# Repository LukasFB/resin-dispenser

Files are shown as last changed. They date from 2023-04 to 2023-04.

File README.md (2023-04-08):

# electronic parts

Arduino Uno (or any other 5V model with I2C and at least 12 free pins)

100g load cell:
https://www.amazon.com/a11112800ux0213-Electronic-Four-wire-Connecting-Weighing/dp/B00880RSTK

HX711 amplifier:
https://www.amazon.com/Comimark-Weighing-Dual-Channel-Precision-Pressure/dp/B07X2JZRKB

2x stepper motor drivers (A4988 is fine, TMC2209 if you're feeling fancy):
https://www.amazon.com/Stepstick-Stepper-Compatible-Printer-Robotics/dp/B09PHD1TR9

2x Nema 17 stepper motors:
https://www.amazon.com/Usongshine-Nema17-Stepper-17HS4401S-Printer/dp/B07KW7F3P9?th=1

2x 100uF capacitors

16x2 LCD with I2C backpack:
https://www.amazon.com/Weewooday-Interface-Backlight-Compatible-MEGA2560/dp/B08MPTND1V?th=1

Toggle switch:
https://www.amazon.com/Nilight-Rocker-Toggle-Switch-Waterproof/dp/B078KBC5VH

4x MX switches

12V, 2A power supply

# mechanical parts
silicone tubing 5mm OD 3mm ID:
https://www.amazon.com/ANPTGHT-Silicone-High-temperature-Brewing-Transfer/dp/B08SQQDZMK?th=1

6x 608 bearings:
https://www.amazon.com/608-2RS-Skateboard-Bearing-Rolling-bearings/dp/B073ST742Z

2x 20 tooth GT2 pulley, 5mm bore:
https://www.amazon.com/3Dman-Pulley-Timing-Aluminum-Printer/dp/B085XLRXS1

2x resin bottles, no bigger than 90x90mm and 220mm tall, about 1 liter:
https://www.amazon.com/Othmro-Plastic-Storage-Container-Translucent/dp/B0828G27TH?th=1

M3 hardware

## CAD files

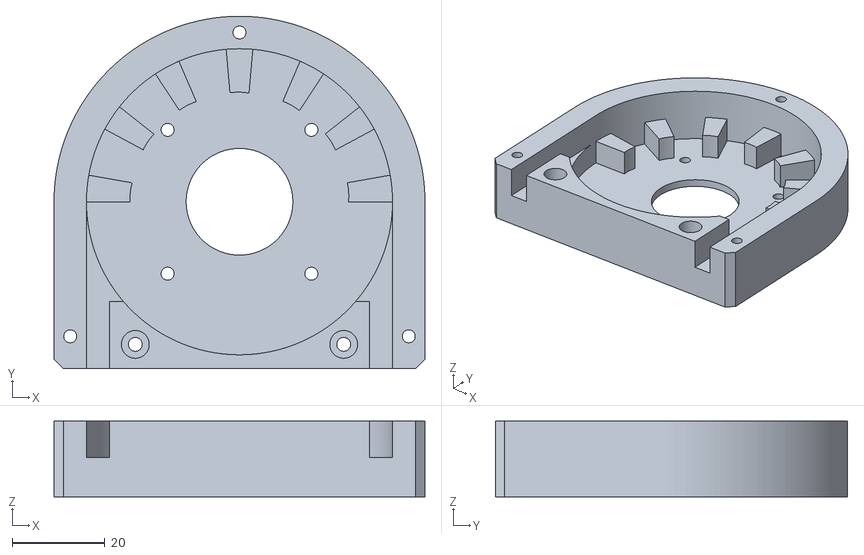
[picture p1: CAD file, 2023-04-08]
printed parts/p_resin dispenser 2 v10_pump_1_housing.stl
80.0 x 76.0 x 16.4

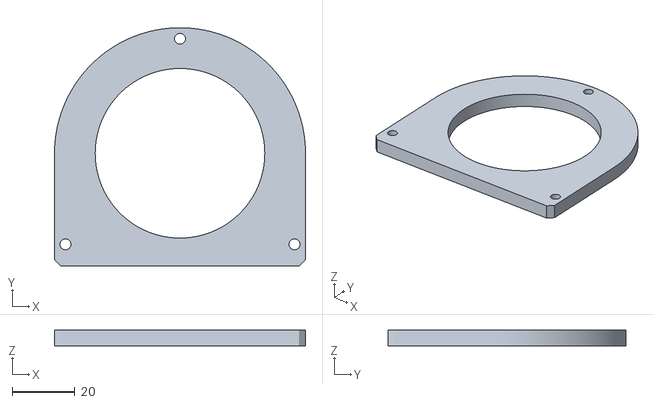
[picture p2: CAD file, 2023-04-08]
printed parts/p_resin dispenser 2 v10_pump_1_cover.stl
80.0 x 76.0 x 5.00

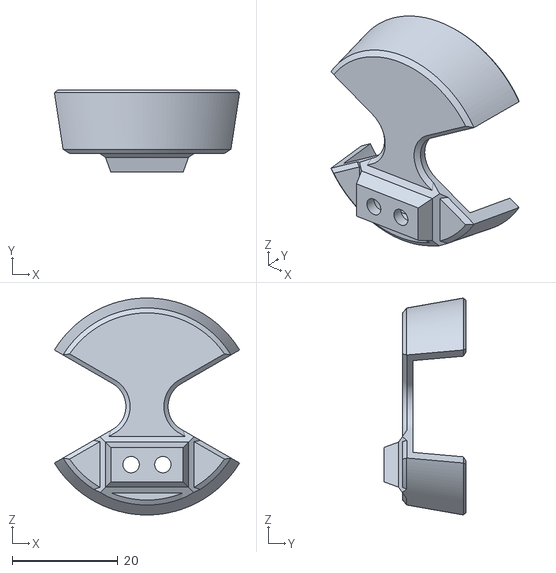
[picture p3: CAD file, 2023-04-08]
printed parts/p_resin dispenser 2 v10_cup_1_bucket upper.stl
35.0 x 15.5 x 41.1

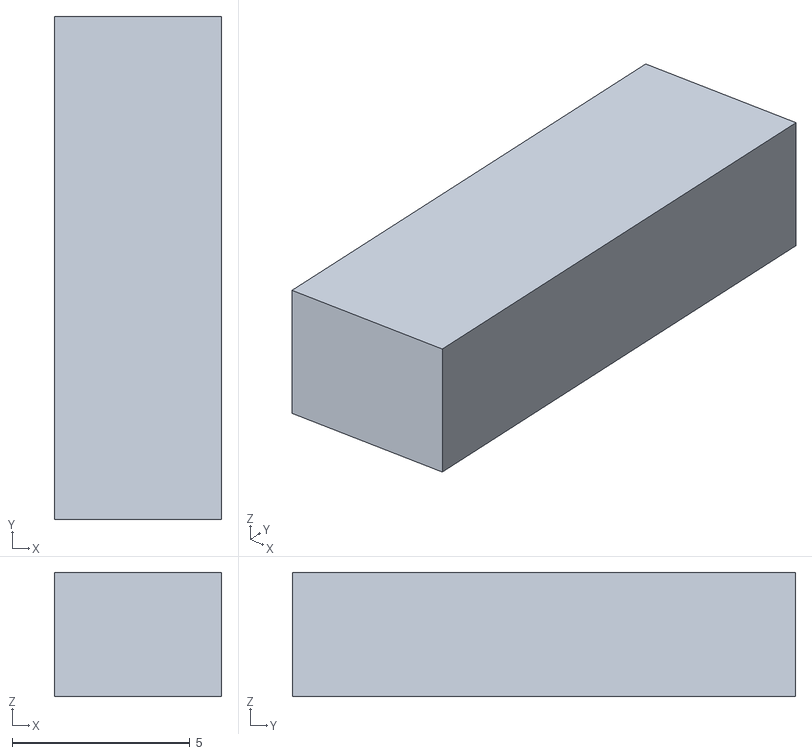
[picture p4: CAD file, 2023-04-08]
printed parts/p_resin dispenser 2 v10_pump_1_tube lock.stl
4.70 x 14.2 x 3.50

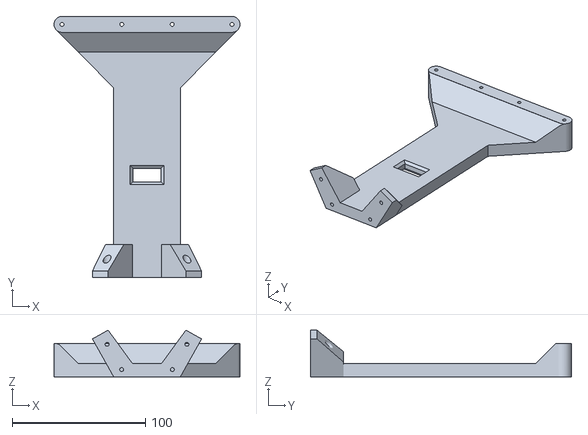
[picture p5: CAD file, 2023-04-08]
printed parts/p_resin dispenser 2 v10_case_1_post.stl
139.7 x 196.2 x 35.1

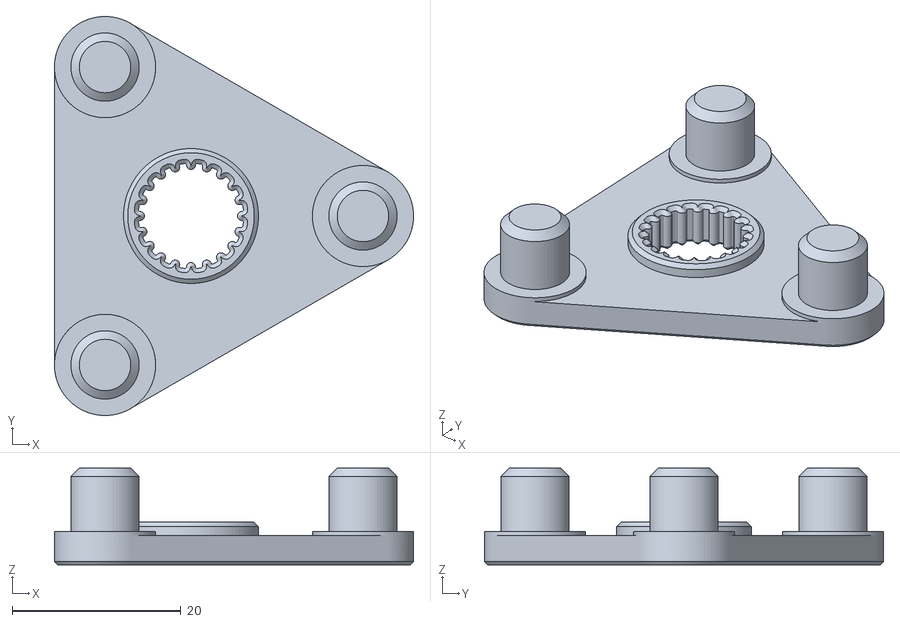
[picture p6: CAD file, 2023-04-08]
printed parts/p_resin dispenser 2 v10_pump_1_spinner.stl
42.6 x 47.3 x 11.5

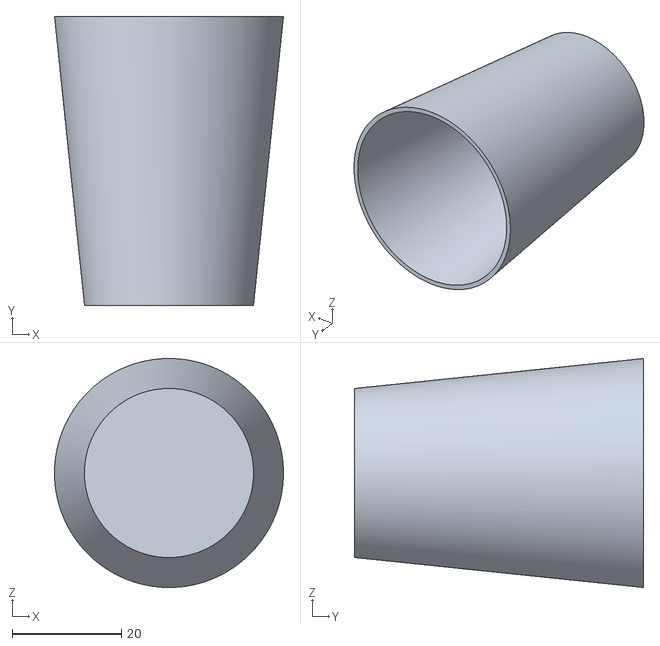
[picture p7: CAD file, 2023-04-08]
printed parts/p_resin dispenser 2 v10_cup_1_cup lower.stl
42.0 x 53.0 x 42.0

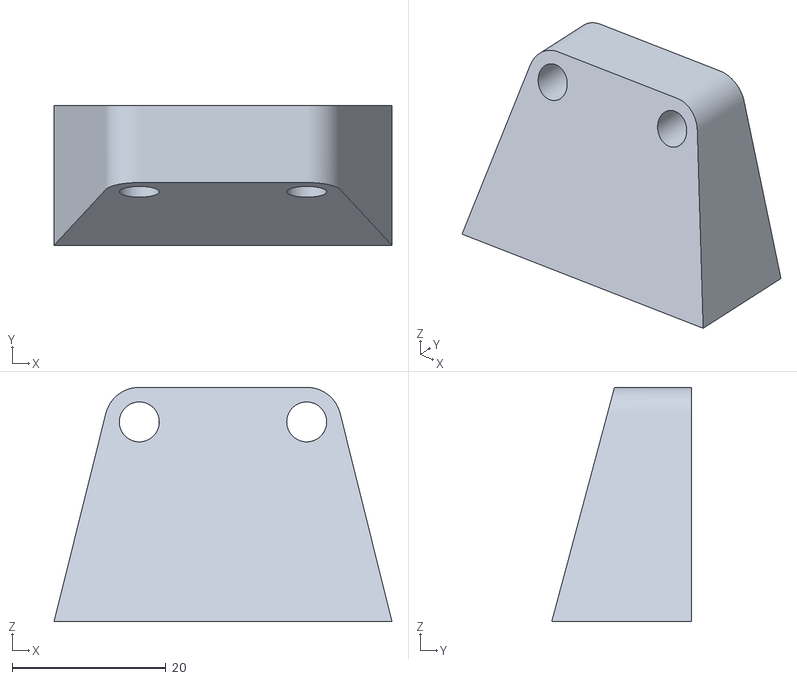
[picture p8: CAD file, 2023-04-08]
printed parts/p_resin dispenser 2 v10_tube holder_1_tube holder.stl
44.0 x 18.2 x 30.5

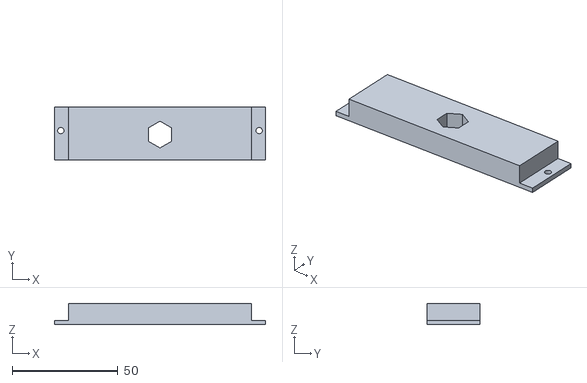
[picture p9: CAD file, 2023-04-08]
printed parts/p_resin dispenser 2 v10_case_1_power cable holder.stl
99.9 x 25.0 x 10.0

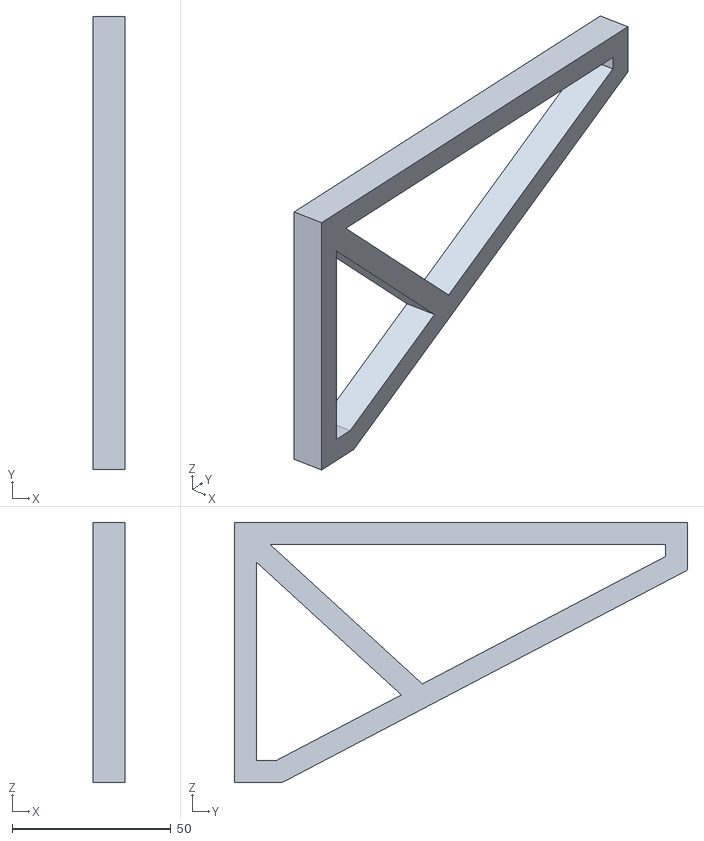
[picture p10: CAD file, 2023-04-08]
printed parts/p_resin dispenser 2 v10_case_1_brace.stl
10.0 x 142.6 x 81.9

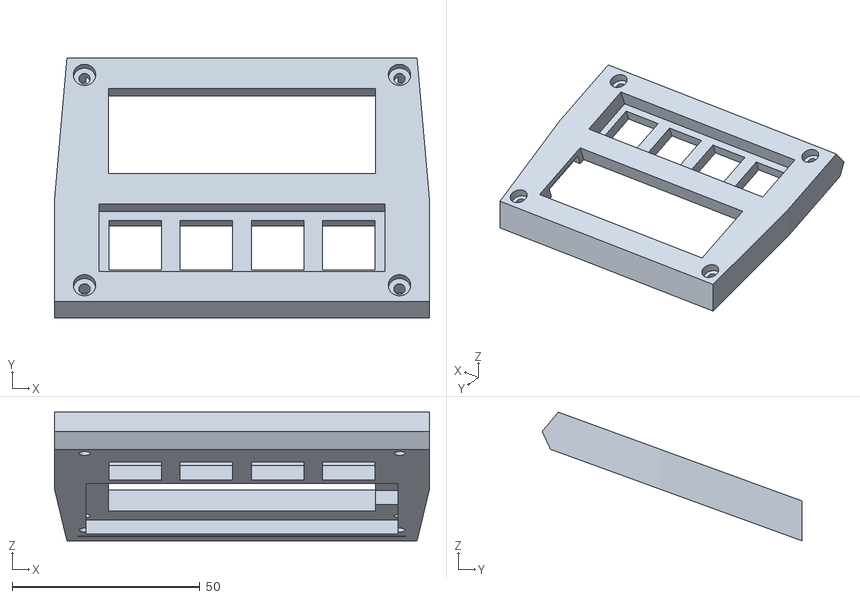
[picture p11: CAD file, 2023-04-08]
printed parts/p_resin dispenser 2 v10_case_1_front.stl
99.9 x 69.2 x 34.3

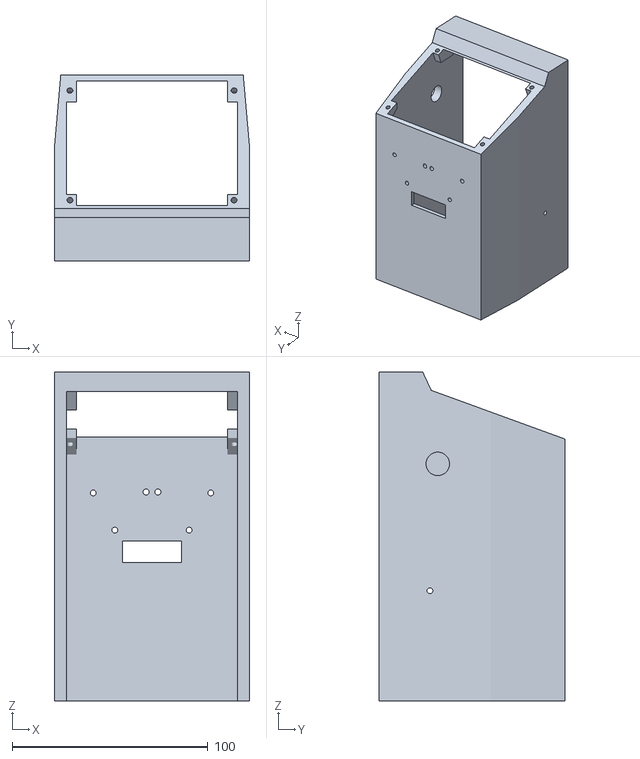
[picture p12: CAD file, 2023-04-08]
printed parts/p_resin dispenser 2 v10_case_1_case center.stl
99.9 x 95.0 x 168.2

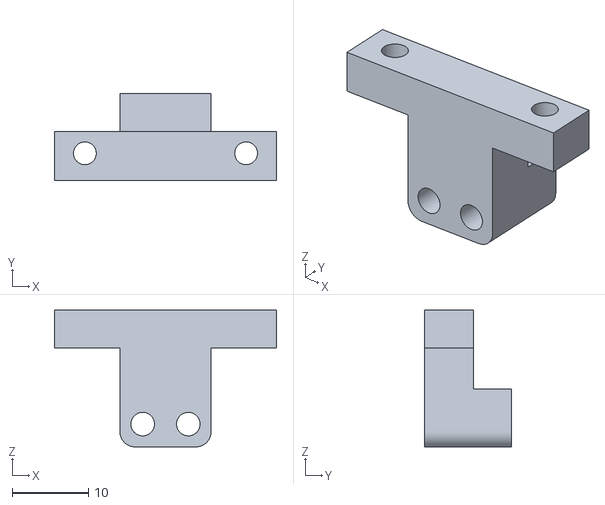
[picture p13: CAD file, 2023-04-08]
printed parts/p_resin dispenser 2 v10_cup_1_load cell bracket.stl
29.2 x 11.4 x 18.0

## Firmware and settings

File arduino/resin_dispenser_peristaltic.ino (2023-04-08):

#include <Q2HX711.h>
#include <LiquidCrystal_I2C.h>
LiquidCrystal_I2C lcd = LiquidCrystal_I2C(0x27, 16, 2);

// setup scale
const byte hx711Data = 2;
const byte hx711Clock = 3;
Q2HX711 hx711(hx711Data, hx711Clock);
float calibrationWeight = 9.415; // << insert the weight of your test object here
float avg_size = 4.0;
float y1 = calibrationWeight;
long x0 = 10700632.0; // << insert values from scale calibration here
long x1 = 10564794.0; // << insert values from scale calibration here
float weightOffset = 0.0;

int btn1 = 10;
int btn2 = 13;
int btn3 = 12;
int btn4 = 11;

int isPressed1 = 0;
int isPressed2 = 0;
int isPressed3 = 0;
int isPressed4 = 0;

int m1Enable = 9;
int m2Enable = 8;
int m1Dir = 7;
int m2Dir = 6;
int m1Step = 5;
int m2Step = 4;

float target = 3.0;
float ratio = 0.6;
float fillEarlyStop = 0.0;

String mode = "main";

int m1Dispense = HIGH;
int m2Dispense = LOW;
int m1Retract = LOW;
int m2Retract = HIGH;

float stepDelay = 1400;
float finalA = 0;
float finalB = 0;

float scaleTara = 0;

void setup() {

  lcd.init();
  lcd.backlight();

  lcd.setCursor(0, 0);
  lcd.print("Starting ...");

  Serial.begin(9600);
  Serial.write("Start ...");

  pinMode(btn1, INPUT_PULLUP);
  pinMode(btn2, INPUT_PULLUP);
  pinMode(btn3, INPUT_PULLUP);
  pinMode(btn4, INPUT_PULLUP);

  // stepper setup
  pinMode(m1Enable, OUTPUT);
  pinMode(m1Dir, OUTPUT);
  pinMode(m1Step, OUTPUT);
  pinMode(m2Enable, OUTPUT);
  pinMode(m2Dir, OUTPUT);
  pinMode(m2Step, OUTPUT);

  digitalWrite(m1Enable, HIGH);
  digitalWrite(m2Enable, HIGH);

  //scaleCalibration(); // << uncomment this once to calibrate the scale
  switchToMode("main");
}

// how much to rotate based on the difference between current and target weight
int getStepsForDiff(float diff) {
  if (diff > 2) return 350;
  if (diff > 1) return 150;
  if (diff > 0.75) return 40;
  if (diff > 0.4) return 15;
  return 5;
}

void loop() {

  checkButtons();

  if (mode == "main") {
    lcd.setCursor(8, 0);
    lcd.print(target);
    lcd.setCursor(0, 1);
    lcd.print(target / (1 + ratio));
    lcd.print(" A");
    lcd.setCursor(8, 1);
    lcd.print(target / (1 + ratio) * ratio);
    lcd.print(" B");
  }

  if (mode == "dispenseA") {

    float current = getScaleReading();
    lcd.setCursor(0, 1);
    lcd.print(current);
    float targetA = target / (1 + ratio);

    if (current > targetA) {
      // reverse motors for a bit, anti drip function
      digitalWrite(m1Dir, m1Retract);
      for (int i = 0; i < 50; i++) {
        digitalWrite(m1Step, HIGH);
        delayMicroseconds(stepDelay);
        digitalWrite(m1Step, LOW);
        delayMicroseconds(stepDelay);
      }
      delay(250);
      finalA = getScaleReading();
      delay(1000);
      switchToMode("dispenseB");
    } else {
      int stepToDo = getStepsForDiff(targetA - current);
      digitalWrite(m1Dir, m1Dispense);
      for (int i = 0; i < stepToDo; i++) {
        digitalWrite(m1Step, HIGH);
        delayMicroseconds(stepDelay);
        digitalWrite(m1Step, LOW);
        delayMicroseconds(stepDelay);
      }
      delay(100);
    }
  }

  if (mode == "dispenseB") {
    float current = getScaleReading();
    lcd.setCursor(0, 1);
    lcd.print(current);
    float targetB = target / (1 + ratio) * ratio;

    if (current > targetB) {
      // reverse motors for a bit, anti drip function
      digitalWrite(m2Dir, m2Retract);
      for (int i = 0; i < 50; i++) {
        digitalWrite(m2Step, HIGH);
        delayMicroseconds(stepDelay);
        digitalWrite(m2Step, LOW);
        delayMicroseconds(stepDelay);
      }
      delay(250);
      finalB = getScaleReading();
      delay(1000);
      switchToMode("result");
    } else {
      int stepToDo = getStepsForDiff(targetB - current);
      digitalWrite(m2Dir, m2Dispense);
      for (int i = 0; i < stepToDo; i++) {
        digitalWrite(m2Step, HIGH);
        delayMicroseconds(stepDelay);
        digitalWrite(m2Step, LOW);
        delayMicroseconds(stepDelay);
      }
      delay(100);
    }

  }
}

void switchToMode(String newMode) {
  mode = newMode;
  lcd.setCursor(0, 0);
  lcd.clear();
  if (mode == "main") {
    // HIGH on able pins = disable motors
    digitalWrite(m1Enable, HIGH);
    digitalWrite(m2Enable, HIGH);
    lcd.print("Target: ");
  }
  if (mode == "dispenseA") {
    digitalWrite(m1Enable, LOW);
    lcd.setCursor(0, 0);
    lcd.print("Filling Part A");
    lcd.setCursor(8, 1);
    lcd.print(" / ");
    lcd.print(target / (1 + ratio));
    delay(250);
    scaleTara = getScaleReading();
  }
  if (mode == "dispenseB") {
    digitalWrite(m1Enable, HIGH);
    digitalWrite(m2Enable, LOW);
    lcd.setCursor(0, 0);
    lcd.print("Filling Part B");
    lcd.setCursor(8, 1);
    lcd.print(" / ");
    lcd.print(target / (1 + ratio) * ratio);
    delay(250);
    scaleTara += getScaleReading();
  }
  if (mode == "result") {
    scaleTara = 0;
    digitalWrite(m1Enable, HIGH);
    digitalWrite(m2Enable, HIGH);
    lcd.setCursor(0, 0);
    lcd.print("Complete");

    lcd.setCursor(0, 0);
    lcd.print(finalA);
    lcd.setCursor(8, 0);
    lcd.print(finalB);

    float realRatio = finalB / finalA;
    float percentage = (realRatio / ratio * 100) - 100;
    lcd.setCursor(0, 0);
    lcd.print("Error ");
    lcd.print(percentage);
    lcd.print(" %");

    delay(5000);
    switchToMode("main");
  }
}

float getScaleReading() {
  // averaging reading
  long reading = 0;
  for (int jj = 0; jj < int(avg_size); jj++) {
    reading += hx711.read();
  }
  reading /= long(avg_size);
  // calculating mass based on calibration and linear fit
  float ratio_1 = (float) (reading - x0);
  float ratio_2 = (float) (x1 - x0);
  float ratio = ratio_1 / ratio_2;
  float mass = y1 * ratio;
  return mass + weightOffset - scaleTara;
}

void checkButtons() {
  if (mode == "main") {
    // increase amount
    if (isPressed1 == 0) {
      if (digitalRead(btn1) == LOW) {
        isPressed1 = 1;
        target += 1;
      }
    } else {
      if (digitalRead(btn1) == HIGH) {
        isPressed1 = 0;
      }
    }

    // decrease amount
    if (isPressed2 == 0) {
      if (digitalRead(btn2) == LOW) {
        isPressed2 = 1;
        if (target > 1) {
          target -= 1;
        }
      }
    } else {
      if (digitalRead(btn2) == HIGH) {
        isPressed2 = 0;
      }
    }

    // start dispensing
    if (digitalRead(btn4) == LOW) {
      switchToMode("dispenseA");
    }
  }
}


void scaleCalibration() {
  delay(1000); // allow load cell and hx711 to settle
  // tare procedure
  x0 = 0L;
  x1 = 0L;
  for (int ii = 0; ii < int(avg_size); ii++) {
    delay(10);
    x0 += hx711.read();
  }
  x0 /= long(avg_size);
  Serial.println("Add calibration weight");
  delay(5000);
  // calibration procedure (mass should be added equal to y1)
  int ii = 1;
  while (true) {
    int r = hx711.read();
    if (r < 5000) {
      Serial.println("no weight ... " + String(r));
      delay(1000);
    } else {
      Serial.println("Calibration mass detected");
      ii++;
      delay(2000);
      for (int jj = 0; jj < int(avg_size); jj++) {
        x1 += hx711.read();
      }
      x1 /= long(avg_size);
      break;
    }
  }
  Serial.println("Calibration Complete");
  Serial.println("x0: ");
  Serial.println(x0);
  Serial.println("x1: ");
  Serial.println(x1);
}
